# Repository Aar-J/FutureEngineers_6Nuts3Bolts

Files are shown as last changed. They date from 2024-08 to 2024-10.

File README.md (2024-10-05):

# Welcome to our GitHub!

# Introduction
We are team 6Nuts3Bolts, a dynamic trio of passionate robotics enthusiasts. 
Based off of the nature of the task, we divded the industry and each took on a key aspect of the challenge.

**Arham**: 

He is in charge of the electronic systems as well as the documentation.

WhatsApp Image 2024-10-04 at 6 19 59 PM

**Shauryaveer**:

WhatsApp Image 2024-10-04 at 6 20 24 PM

He is our main designer and constructor and worked on the car's mechanisms

**Ranveer**: 

WhatsApp Image 2024-10-04 at 6 20 25 PM

He is our programming lead, and responsible for all the code and processing on our robot.

**Team Photo**:

Untitled design (48)

Untitled design (49)

# Table of Contents
Car photos

Vehicle Videos
- Open Round
- Obstacle Round

Our Engineering Process

- Fundamental Parameters
- Mobility Management
  - Explanation
  - Iteration Process
  - How we achieved our target
  - Improvements
  - Parts list

- Power and Sense Management
  - Explanation
  - Iteration Process
  - How we achieved our target
  - Improvements
  - Parts list
    
- Obstacle Management
  - How we achieved our target
  - Explanation
  - How we achieved our target
  - Future Improvements
  
Acknowledgement to our mentor Sahil Gajera Sir

Thank you to the judges

# Car Photos

### Top View

Untitled design (42)

### Bottom View

Untitled design (43)

### Front View

Untitled design (44)

### Back View

Untitled design (45)

### Left side 

Untitled design (46)

### Right Side

Untitled design (47)

# Vehicle Videos
### Open Round
https://www.youtube.com/watch?v=metChoJu9pQ

### Obstacle challenge
https://www.youtube.com/watch?v=metChoJu9pQ

# Our Engineering Process
We have used scoring criteria from the ruleblock as headings in our documentation to make it easy to navigate our repository.

It is vital to understand a problem and its features in depth before planning and undertaking its solution. Hence, we first spent a day analysing the challenge in depth and noting down a few principles, parameters, fundamental ideas off of which we could organize our thinking and streamline our ideation process to efficiently solve the challenge. 
Here are the principles we decided on:

## Fundamental Parameters
**Design and Construction**
- Compact, able to maneuver past obstacles even at high speeds
- Simple and practical, a design appropriate for the challenge, not overly complex
- Modular, quick and easy to assemble and disassemble

**Electrical Systems**
- Clean and orgranised, connections easy to keep track of
- Reliable and safe, eliminate any chances of a short or circuit failure
- Easy to assemble and dissassemble

**Logic and Programming**
- Simple and organized
- Easy to navigate, debug and troubleshoot
- Flexible, able to evolve easily to overcome any issues or edge cases

Based off these fundamental ideas, we aimed to conceptualize our robot.
Next, we immediately begain the prototyping and iteration process.

Here's how we went about turning our vision into reality

## **Mobility management**

### Explanation

**Why we chose the RevRobotics NEO550**

Untitled design (15)

- It has an absolutely phenomenal power to weight ratio (weighing only 140grams and has a peak output power of 279W) as well as very high acceleration and has a free running speed of upto 11000 RPM.   We have geared it in a 5:1 ratio. This can further be seen through this graph

Untitled design (59)

- We had previously used this motor in FRC (FIRST Robotics Competition) and hence were comfortable operating with it.
- It has excellent speed control and is easy to integrate and program with the SparkMax motor controller.
- We had initially considered making a smaller robot and at the time had considered using an N20 500 RPM Encoder motor, however this placed a lot of restrictions on our other electronics and design. We also considered using a standard Johnson 500 RPM motor, or a TT Gearbox motor however we rejected these for similar reasons as well as the fact that the NEO 550 just outclassed all 3

**Why we chose MG996R Servo**

Untitled design (17)

- It is a popular and reliable servo which for us is delivering about 9.5kgcm(since we are powering it through the RaspberryPi 5V pin)
- It is easily able to steer our robot even at high speeds.
- The position accuracy it is able to provide is relaible and it is able to steer at a rate of about 0.30 sec/60° degrees according to our measurements.

**Electronics Mounting Plate** 

Untitled design (22)

Untitled design (29)

The electronics table offers ample space for organizing wiring effectively. It is spacious enough to accommodate most of the wiring, ensuring everything remains well-organized and accessible for easy maintenance and troubleshooting.

**Top Plate**

Untitled design (23)

Untitled design (31)

The top plate is the strongest and most robust part of the robot, serving as its backbone. 

It plays a vital role in every subsystem, providing structural integrity and supporting the entire design.

**Bottom Plate**

Untitled design (24)

Untitled design (30)

The bottom plate provides essential support and serves as a key aesthetic feature for the robot. It protects the belly of the robot from potential damage while also adding significant structural integrity to the overall foundation. By ensuring a strong base, the bottom plate helps maintain the robot's durability and stability during operation. Its role in reinforcing the lower framework makes it a critical component of the robot's design.

**Bevel Gears**  

Untitled design (25)

Untitled design (32)

The bevel gears are designed for durability, featuring a large diameter and sizable teeth. This design ensures they wear out more slowly, making them reliable and long-lasting components of the drive system.

**Motor Bracket**  

Untitled design (26)

Untitled design (33)

The motor bracket is small and simple in design, effectively performing its function without occupying excessive space. 
It optimizes space utilization while ensuring the motor is securely mounted.

**Camera Mount**  

Untitled design (28)

The camera mount is tall and adjustable, providing flexibility in positioning without taking up much flat space on the electronics table. It offers several customization options to fit various configurations as needed.

**Steering System**  

Untitled design (27)

Untitled design (34)

The steering system is compact and straightforward, featuring a linkage-based design. It allows for the maximum possible steering angle and is highly reliable, ensuring excellent maneuverability and performance.

### Iteration process
We went through 4 iterations of the design. Here's a bit about them.

**Version 1**



We began with a simple, open chassis design that provided ample space for future electronics and cabling, offering flexibility to adjust the layout as needed.

The motor and electronics were placed centrally to maintain balance and reduce the risk of tipping during movement.

The flat and spacious base was designed to simplify assembly and allow easy access to key components.

For the steering system, we initially used an approximate Ackermann configuration to improve cornering performance by adjusting wheel angles based on turning radius.

After evaluating the robot’s performance, we switched to a linkage-based steering system, which offered more straightforward control with fewer mechanical components, minimizing potential points of failure.

We integrated the bulky Limelight camera, mounting it high on a custom bracket to ensure optimal visibility for the robot's vision systems.

Although the camera’s size was disproportionate to the compact robot, we relied on it for initial tests due to its accuracy in target detection and our team's familiarity with its setup.

The camera placement was chosen to minimize interference from the robot's body and ensure accurate visual data capture.

This design iteration allowed us to explore several improvements for future versions, including lowering the base height to reduce the robot's center of gravity and increase stability,
transitioning to a layered architecture for better component arrangement and improved separation of electronics, minimizing signal interference, and
trimming excess space in the length and width of the frame to create a more compact and efficient design, maximizing maneuverability without sacrificing functionality.

**Version 2**



In this iteration, we focused on making the design more compact and practical, even if it introduced some complexity.

Unlike the modular and adjustable nature of Version 1, this design was fully customized for the specific requirements of the use case.

The first major decision was to align the motor with the length of the robot, significantly reducing the overall width.

To achieve this, we implemented a 90-degree power transmission system using custom-designed, 3D-printed bevel gears (approx. 2 cm in diameter).

The custom motor mount could also house a REV Through Bore Encoder to measure back wheel rotations, but we decided it wasn’t necessary for this version.

We introduced a layered structure with three levels:

The top layer was exclusively for the electronics.

The lower layers housed wiring, the SPARK MAX controller, and other components.

After finalizing the battery choice, we built the robot layout around it to ensure proper space allocation and balance.

The electronics board was designed to be hot-swappable, allowing it to snap into place without screws, so electronics development could be done separately and easily integrated.

We also implemented a simple linkage-based steering system, powered by the MG996R servo, improving steering control while keeping the design compact and efficient.
The transition from Version 1 to Version 2 marked a significant leap, making the robot more space-efficient and purpose-built for the specific application.

**Version 3 (Abandoned)**



In this version, we aimed to make the robot as small as possible, accommodating every element efficiently.

The chassis width was reduced to 8.4 cm (down from 10 cm), significantly improving maneuverability.

The overall height was also reduced, and although ground clearance wasn’t a priority, it was slightly improved for potential ground-facing sensors.

Early in the design, we realized shrinking the dimensions came with trade-offs.

The maximum turning angle of the steering wheels was reduced by 10-15 degrees on either side.

The servo had to be placed in an unconventional manner.

To address these issues, we explored adding 5-6 layers to the design to distribute components while keeping the robot compact.

Despite our efforts, feedback from testing Version 2 showed that width wasn’t a major concern, and while this version was sleeker, it presented too many complications.
The layered structure created challenges in both assembly and component access, making the design overly complex.

From this iteration, we learned that the current dimensions were already optimized, and future designs would likely stay within a tolerance of ±2-3 cm.

Making the robot smaller worsened the wiring complexity, as the compact spaces made routing cables and connections more difficult to manage.

This realization helped us pivot back to a more practical sizing while still focusing on overall efficiency.

**Version 4**



In this version, we started from scratch, incorporating lessons from previous iterations.

The width remained unchanged, but the length was significantly reduced.

We transitioned from a 20:1 UltraPlanetary gearbox to a 5:1 system, which, along with steering modifications, allowed us to achieve our most compact design yet.

The electronics table at the top was made wider, extending beyond the chassis but staying within dimensional constraints.

We moved away from the hot-swappable top plate design, as the snap-on system weakened after repeated use and occasionally broke off.

The bottom plate was refined to remove unnecessary parts and featured our team name cut out for weight reduction and aesthetic appeal.

The middle plate now carried the bulk of the structural load, becoming the backbone of the robot. The thickness of both the bottom and middle plates was increased from 3mm to 4mm, greatly improving strength and eliminating flex.

A key improvement was in the drive subsystem, during test runs, we noticed vibrations while turning, due to the lack of a differential system.
The inside and outside wheels rotated at the same speed, causing a mismatch.
To fix this, we reduced the gap between the wheels, minimizing vibration in a simple manner.
We also upgraded the bevel gears, increasing their size from 2 cm to 3 cm in diameter.
This made the gears much stronger, eliminating wear-and-tear issues.

Previously, we had to replace the smaller gears after every five runs, but with the new design, frequent replacements were no longer necessary.

Overall, this design marked the culmination of all our ideas and refinements, making it the most optimized and efficient version yet, combining technical improvements with practical design choices.

**Key Differences between the versions**
| **Aspect** | **Version 1** | **Version 2** | **Version 3 (Abandoned)** | **Version 4** |
|---|---|---|---|---|
| **Chassis Design** | Simple, open chassis with spacious flat base for flexibility | Compact and customized, 90-degree power transmission via bevel gears | Extremely compact, 8.4 cm width; 5-6 layered design; trade-offs in turning radius | More compact than v2, width unchanged, reduced length |
| **Motor Placement** | Central for balance | Aligned with the length, bevel gears for 90-degree power transmission | Motor placement compromised for size | Same as v2, with more robust gearing system |
| **Steering System** | Approximate Ackermann, later switched to linkage-based | Linkage-based, powered by MG996R servo | Reduced turning angle due to compactness | Linkage-based with further steering modifications to reduce size |
| **Electronics Layout** | Spacious, simple arrangement on a general-purpose board | Layered design with three levels, hot-swappable electronics board | 5-6 layers proposed, overly complex, compact | Wider electronics table, no hot-swappable design due to durability issues |
| **Camera System** | Limelight camera, large and mounted high for optimal visibility |Limelight Camera Swapped for RaspberryPi Camera| Same as v2, camera mount strengthened | Same as v3 |
| **Frame Dimensions** | Spacious, flexible for adjustments | Narrower (due to motor alignment) and more layered | Extremely compact (8.4 cm width), but overly complex | Reduced length, width unchanged; optimized overall dimensions |
| **Gearbox** |20:1 UltraPlanetary gearbox |Same as v1 | Same as v2 | Switched to 5:1 UltraPlanetary gearbox for compactness and speed|
| **Bevel Gears** | Not used | 2 cm diameter, custom 3D-printed | Same as v2, but layering increased difficulty | 3 cm diameter, stronger, reduced wear and tear |
| **Material Strength** | Standard 3 mm plates | Standard 3 mm plates | Same as v2 | Plates increased from 3 mm to 4 mm for improved structural strength |
| **Vibration Control** | We discovered the vibration issues | No differential system, resulting in vibrations | Working on v4 since v3 was abandoned| Reduced wheel gap to minimize vibrations during turns |
| **Testing and Feedback** | Preliminary tests with bulky camera setup | Refined design with specific components, partial finalization | Abandoned due to complexity, compromised steering, and wiring issues | Final optimized version, most refined in terms of design and performance |
| **Complexity** | Simple and flexible | More complex but optimized for purpose | Extremely complex and impractical | Balanced complexity with practical refinements |

### How we achieved our target

**How we made it Compact**

More well positioned Cardboard Plate (3)

We began by visualizing how all the components could fit closely together, and we built around that idea. The space between parts is minimal, but we made sure it wouldn’t create any issues in performance or accessibility.
The overall length of the robot is limited by key components like the NEO 550 motor, bevel gears, and the steering system, while the width is determined by the size of the Spark MAX, ultrasonic sensor, servo, and battery. By carefully balancing the length and width, we were able to create a robot that is compact yet fully functional. The width isn't constrained by any specific part, it’s simply as wide as necessary to accommodate the essential components.

**How we ensured simplicity and practicality**

From the beginning, we adopted a mindset of keeping things simple. We've learned that complexity can quickly lead to chaos, especially when time is tight or you're troubleshooting under pressure. By focusing on simplicity, we narrowed our options and only considered ideas that were practical and easy to implement. If a solution met our goals without adding unnecessary complications, we ran with it. Simplicity also naturally led to practicality because fewer moving parts meant fewer things to go wrong, and every design choice was intentional and straightforward.

**How we made it Modular**

The entire robot is based around three main plates, with each subassembly between them individually 3D printed. This modular design gives us a lot of flexibility. In case something goes wrong with a specific part, we don’t need to overhaul the entire system—just swap out the problem area. It makes troubleshooting and maintenance much quicker and less stressful.
We designed the robot to be broken down into three key systems: the drive system, the steering system, and the electronics assembly. Any part that doesn’t fall into one of these categories is mostly there to provide structural integrity and support to the main components. For instance, the bottom plate doesn’t serve any critical function other than strengthening the overall structure. This modular approach ensures that our robot remains easy to work on, upgrade, and maintain, which is key for long-term reliability.

### Future Improvements
If we had more time, we would likely explore a more complex design that branches off from the v3 concepts while integrating elements from the v4 robot. This hybrid approach would allow us to capitalize on the strengths of both iterations, leading to an ideal robot that embodies our design philosophy. By merging the compact efficiency and structural integrity of v3 with the advanced features and refined functionality of v4, we could create a robot that maximizes performance while enhancing maneuverability and adaptability. This exploration could involve developing a more sophisticated drive system or experimenting with innovative materials and configurations to further reduce weight and improve responsiveness. Ultimately, this integration of ideas would help us push the boundaries of our design capabilities and achieve our vision of an optimal robot tailored to our specific needs.

### Hardware Components list:
- Rev Duo 60mm Traction Wheels https://www.revrobotics.com/DUO-Traction-Wheels/
- **Chassis**
  - **Top plate**
  - **Bottom Plate**
- **Steering Mechanism**
  - **Linkage**
  - **Left Front**
  - **Right Front**
- **Bevel Gears**
- **Motor Bracket**
- **Electronics Mount**
- **Camera Mount**
- **1 x Servo horn** (comes with servo)
- **20 x m3 10mm bolts** https://robokits.co.in/robot-parts/nut-bolts-standoffs/allen-cap-socket-head-bolts/m3-x-10-mm-socket-head-cap-stainless-steel-304-bolt-moq-15-pcs
- **2 x m3 30mm bolts** https://robokits.co.in/robot-parts/nut-bolts-standoffs/allen-cap-socket-head-bolts/m3-x-30-mm-socket-head-cap-stainless-steel-304-bolt-moq-15-pcs
- **16 x m3 nyloc nuts** https://robokits.co.in/robot-parts/nut-bolts-standoffs/nuts/m3-nyloc-nuts-304-stainless-steel-moq-25-pcs
- **1 x 90mm shaft** https://www.revrobotics.com/5mm-Hex-Shafts/#REV-41-1348-PK4
- **1 x 20mm shaft** (can be cut from longer shaft)
- **2 x shaft collars** https://www.revrobotics.com/rev-41-1327-pk10/
- **4 x 60mm rev wheels** https://www.revrobotics.com/DUO-Traction-Wheels/#REV-41-1350-PK4

## **Power and sense management**

## **Explanation**

### Reason for choice of parts

**RaspberryPi 4B**

Untitled design (35)

- With its quad-core ARM Cortex-A72 64-bit 1.5GHz processor and 8GB RAM it meant that we would never face a computationl bottleneck, even with the heavy task of image processing in the obstacle         challenge.
- Its ability to be programmed and controlled wirelessly was a boon during the testing and debugging phase as we could run the robot almost continuously without having to detach and reattach            the cable for uploading code.
- Its extensive use and testing was the reason we chose to go with the RaspberryPi 4B instead of the newer RaspberryPi 5. If there was ever an issue we faced, it could most likely be solved by          searching up the problem.

**RaspberryPi Camera Module 3 with Wide Angle lens**

Untitled design (36)

- We chose this mainly for its ease of integration and compatability with the RaspberryPi. 
- Its wide FOV (120 degrees), high resolution(12 megapixels), autofocus feature and ability to sense color in a wide range of lighting conditions allowed for efficent obstacle detection and             sensing from varying distances and angles even while moving at high speeds

**Arduino Nano**

Untitled design (37)

- The use of the Arduino Nano in our robot is solely to gather data from the ultrasonic sensors and relay it to the RaspberryPi. 
- Hence its compactness and low power consumption was the main reason we chose to use it.

**BNO055 IMU**

Untitled design (38)

- The BNO055 is a highly tested and reliable sensor. We had used it earlier in FTC(First Tech Challenge) as well as in a drone we made. We had also used it in Future Engineers the previous year.
- It has an inbuilt sensor fusion algorithm and it is easy to integrate with the RaspberryPi, communicating over I2C.

**RevRobotics SparkMax Motor Controller**

Untitled design (18)

- Using the NEO550 meant we would have to use this since they are complimentary pieces of hardware.
- Its inbuilt current limiting feature also allows for the motor to remain safe from sudden power surges.

**HC-SRO4 Ultrasonic Sensors**

Untitled design (14)
- These are widely available and a popular choice of sensor although sometimes they may be unreliable, with good programming they can be made to work just fine. 
- There are many resources and libraries available online to control these effectively making both programming and troubleshooting easy to do.
- Their accuracy is reasonable, able to provide output within a 2-3mm range of error and are also able to maintain consistency at moderate speeds, providing data every 30ms.
- Apart from that, its also easy to integrate

**Xcluma USB Buck Converter**

Untitled design (16)

- It was able to provide a more stable output of 5V than the buck converter we were previously using. It also made it such that we could easily power the RaspberryPi through its USBC port.
- It was also more compact than the previous buck.
- Its built in safety feature of preventing against overvoltage and overcurrent proved to be useful especially during testing.

**2200MAh 40C 12V LiPo Battery** 

Untitled design (39)

- We needed a high power battery since the electronic components we used(RaspberryPi while image processing, NEO550) were quite power hungry.
- It was also capable of providing our robot with a long runtime. We can run our robot for 12 minutes continuously.

### Circuit Schematic

WRO Future Engineers Circuit Schematic

### Iteration Process

**Version 1**

This was a prototyping version, simply to test the circuit and have a robot capable of moving while we worked on a better one. This was for version 1 of the design.
It consisted of the Electronics mounted on a cardboard plate and the use of a prototyping board fundamentally composed on 4 buck converters. There were wires going everywhere, even outisde the perimeter of our bot. However, this was only ever meant to be a prototyping version. 

Carboard Plate (1)

**Version 2**
This was also merely a prototyping version intended on having a functional robot to program. The difference between Version 1 and 2 is solely the cleanliness of the mounting and the organization of wires. This was mostly in place during versions 2 and 3 of our desgn

The Crius power distribution board was a cool piece, however it was ultimately redundant. It consumed space, as well as had excess ports which we had no use for. Hence it was discarded. 
The fuse we were using had a rating of 15A. Our circuit will never draw more than 4A hence this was also unnecessary.
The cardboard plate mounting although humble, actually surprised us as it turned out to be quite solid and reliable. However we  knew that having a proper circuit board would yet be a better decision.

More well positioned Cardboard Plate (2)

**Version 3**

Untitled design (60)

We were always planning on soldering all the components onto one single board for the final iteration of our robot, however due to changes in components as well as troubleshooting, we waited till all our systems were finalised before making our circuit board. This is what we used for version 4(final) of our design

This is (at leat for nationals) the final iteration of the electrical systems of our robot. It is a significantly improved version and has all the electronics mounted on a general purpose board. It provides a clean and professional look to our robot and also minimises wiring mistakes as well as chances of shorts. 

### **How we achieved Clean and Organized wiring**

To keep our wiring system easy to manage, we focused on clarity, organization and structure in all connections.

More well positioned Cardboard Plate (4)

We used solid core wire for connections since they can be bent into shape making wiring neat and easy to solder.
We soldered all wire connections and mounted them on a general purpose board providing a solid foundation for the wiring, minimizing loose wires and clutter.
Every wire was labeled and color-coded, making it simple to track individual connections. This helped ensure quick identification of components during assembly and troubleshooting.
  
Red - VCC wires 🟥

Black - GND wires ⬛

Purple - PWM Signal (Pin 33 or GPIO 13 on RaspberryPi) 🟪

Yellow(Ultrasonic) - TRIG (Pins D3 and D7 on Nano) 🟨

Blue(Ultrasonic) - ECHO (Pins D4 and D6 on Nano) 🟦

Yellow(BNO055) - SDA (Pin 3 or GPIO 2 on RaspberryPi 🟨

Blue(BNO055) - SCL (Pin 5 or GPIO 3 on RaspberryPi) 🟦

Blue(Button) - SIGNAL (Pin 11 or GPIO 17 on RaspberryPi) 🟦 

Black and White Dual Wire(SparkMax Communication) - ⬛⬜ (Pin 33 GPIO 18 and Pin 34 or Ground)
    
### **How we ensured Reliability and Safety**

We took extra care in insulating all exposed connections to prevent shorts or malfunctions. 

Untitled design (53)

This was done to all soldered connections by applying heat-shrink tubing, hot gluing wire ends and using 
electrical tape wherever required for additional protection and to reinforce connection stability.
We used barrier terminal blocks and JST connectors which hold the wires firmly in place thus preventing them from moving around and accidentally causing short circuits or bending of wires.
Wago connectors were used for connections between the SparkMax and Neo ensuring a tight and insulated fitting.
    
### **How we made it convenient to assemble and dissasemble**

Untitled design (61)

Ease of maintainence and assembly was another top priority. 

We soldered header pins onto the general purpose board in order to render the Arduino Nano, BNO055, and servo easily detachable and replaceable.
The screw in nature of the barrier terminal blocks not only added a layer of security to our electrical system but also served as a way to ensure quick maintanence. The wires can be removed and reattached by simply screwing and unscrewing the terminals. 
A similar story is for the the JST connectors, their ability to snap in place makes it easy to attach and detach the ultrasonic sensors.
Wago connectors are convenient to make connections with components where cutting the wiring and making solder joints is not preffered due to the wire being inbuilt into the component like the SparkMax and NEO550.
We also used crimp connectors for the switch, such that we could quickly remove and replace it if necessary since we had faced issues during practice of the switch being unreliable

### Future Improvements

- We plan on using PCB Design software to create a circuit design and then have that PCB printed and manufactured. This will almost completely eliminate     small wired connections and chance of circuit failure.
- We also plan on swapping out the HC-SR04 Ultrasonic sensors with faster and more reliable ones like the URM09 or SEN001.
- We may also swap out the RaspberryPi for a more powerful controller like the Jetson Nano

### Electrical Components list:
- **RaspberryPi 4B**
  https://robu.in/product/raspberry-pi-4-model-b-with-4-gb-ram/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
  
- **Raspberry Pi Camera Module 3 with Wide Angle Lens**
   https://robu.in/product/raspberry-pi-camera-module-3-wide/
  
- **Arduino Nano**
  https://robu.in/product/arduino-nano-board-r3-with-ch340-chip-wo-usb-cable-solderedarduino-nano-r3-wo-usb-cable-soldered/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        
  gad_source=1&gclid=CjwKCAjwgfm3BhBeEiwAFfxrG2RzmpzoTJQA5ThT4OKJQDOLGdDu_CcdCzMTJhiYnkzNB_LoFYl8ChoCa28QAvD_BwE
  
- **BNO055 IMU**
  https://evelta.com/7semi-bno055-9-dof-absolute-orientation-sensor-breakout-i2c-qwiic/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
  
- **MG996R Servo**
  https://robu.in/product/towerpro-mg996r-digital-high-torque-servo-motor/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
  
- **RevRobotics NEO550**
  https://www.revrobotics.com/rev-21-1651/
  
- **RevRobotics SparkMax Motor Controller**
  https://www.revrobotics.com/rev-11-2158/
  
- **HC-SR04 Ultrasonic Sensors**
  https://robu.in/product/hc-sr04-ultrasonic-range-finder/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
  
- **Xcluma USB Buck Converter**
  https://www.xcluma.com/0.9v-5v-to-5v-600ma-usb-output-charger-step-up-power-module-mini-dc-dcboostconvertergad_source=1&gclid=CjwKCAjwgfm3BhBeEiwAFfxrGwnZnr6HztAhUfI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
  
- **2200MAh 40C 12V LiPo Battery**
  https://robokits.co.in/batteries-chargers/drone-batteries/genx-power-premium-lipo-battery/genxpower-11.1v-lipo-batteries/genx-11.1v-3s-2200mah-40c-80c-premium-lipo-l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
  
- **Switch**
  https://robu.in/product/kcd5-101-mini-rocker-switch-2pinon-off/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
  
- **Pushbutton**
https://robu.in/product/mc002076-terminal-block-barrier-3pos/
  
- **General Purpose Board**
  https://robu.in/product/8-x-12-cm-universal-pcb-prototype-board-single-sided-2-54mm-hole-pitch/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
  
- **JST Connectors**
  https://robu.in/product/4-pin-jst-xh-2-54mm-pitch-plug-and-socket-with-cable-5-pcs/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
  
- **Jumper Wires**
  https://www.amazon.in/Electrobot-Jumper-Wires-120-Pieces/dp/B071VQLQQQ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
  
- **Solid Core Wires**
  https://robocraze.com/products/single-stranded-hook-up-wires-1m-each-5-colorsvariant=40193905590425&currency=INR&utm_medium=product_sync&utm_source=google&utm_conten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
  
- **XT60 Connectors**
  https://robu.in/product/amass-xt60-male-connector-xt60-m-g-y/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
  
- **Crimp Connectors**
  https://www.tsktech.in/product/6-3mm-female-spade-connector-with-insulator-boot-crimp-terminal-thimbles-no-color-choice-pack-of-10nos/
  
-**Wago Connectors**

 https://www.flipkart.com/wago-2-conductor-compact-inline-splicing-connectors-electrical-wire-connector/p/itmd8735b383bb17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

## **Obstacle management**
In this sections first we will first discuss how we solved the obstacle challenge and then move onto the  solution for the open round challenge as well as a general explanation of our software and logic flow.

### Explanation

#### **Obstacle Challenge**

First we begin by importing all the libraries



import time 
- The time library, as the name suggests allows us to use time related functions like delays.



import board
- Its use is primarily to access pins on the RaspberryPi.



import busio
- This library allows us to access external buses and serial protocols allowing for hardware acceleration on the RaspberryPi.



import adafruit_bno055   
- Library for BNO055 IMU sensor



import sys
-  This library basically allows us to run functions and call from different files and parts of code. Its gives us commands to access system related variables and functions.



import serial  
- This allows for serial communication with external devices. We communicate with the Arduino Nano over serial



sys.path.append('/usr/lib/python3/dist-packages')  
- We have created custom packages for the left journey and right journey of the open round. Both are called. The robot must decide which one to run.


  
import pigpio   
- The RaspberryPi's software PWM signal is often unstable and unreliable. The pigpio library solves this issue generation a hardware PWM on the the         
  RaspberryPi.



from picamera2 import Picamera2, Preview  
- Camera library for handling the Raspberry Pi camera



import cv2  
- Here we are importing OpenCV for camera processing and display. This handles all of the vision processing.



import numpy as np
- Here we import NumPy for numerical operations using it in conjunction with OpenCV for image data processing.



import Blue_detected as b1
- This is a custom module containing functions for color detection.

Next we set up all the communication protocols, declare all the control variables in our program and initialise the necessary objects. 
We will use these to build our logic.



- We create a Picamera2 object to handle camera operations.
  
- The video configuration is set to a resolution of 640x480 pixels, with a frame duration limit of 33.33 milliseconds, which corresponds to 30 frames per second.
  
- The camera is then started, preparing it to capture images.



pi = pigpio.pi() 
- Initializes the pigpio library for GPIO control



pi.set_mode(18, pigpio.OUTPUT)  
- Set GPIO pin 18 as an output (for NEO550 Motor)
  
pi.set_mode(13, pigpio.OUTPUT) 
-  Set GPIO pin 13 as an output (for MG996R Servo)



i2c = busio.I2C(board.SCL, board.SDA)   
- Initializing I2C bus for communication with the IMU



ser = serial.Serial('/dev/ttyACM0', 9600)  
- Setting up a serial connection to an external device (Arduino Nano) at 9600 baud rate



sensor = adafruit_bno055.BNO055_I2C(i2c)  
- Initializing the BNO055 sensor using I2C



heading = 0.0   
- To store the heading (direction) from the IMU sensor


  
dis = 0.0  
- To store the distance from the left sensor
  

 
value = 360 
- Value to control servo/motor position



count = 0  
- A counter to count number of loop iterations



arR = arG = yy = xg = xr = 0
- These are variables for color detection areas.



orange = False
- Flag variable for if orange color is detected.



increment = False  
- Flag for controlling incremental behavior



flag = True  
- Flag variable to track state



init = True  
- Flag variable to track initialization state

PID Controller

Here we initialise our PID function



The input parameters for the PID Controller are :

**y** 
- This is the target heading or the direction you want the robot to face.
  
**heading** 
- This stores the current heading of the robot, i.e., the direction the robot is currently facing, measured by the BNO055 sensor.
  
**kP**
- This represents the proportional constant used to determine how much correction to apply based on the error. The higher the constant, the more   
  aggressively the robot will correct its heading.
  


Here we normalize our "y" or target heading.
- This part ensures y is normalized within the range of -180 to 180 degrees.
  
- The idea is to convert the heading into a more manageable format that can be used for comparison and calculation.
  
- If y is less than 360 - y, it remains unchanged.
  
- If y == 360 - y, meaning it’s exactly opposite (180 degrees), it's set to 180 degrees.
  
- Otherwise, it subtracts y from 360, effectively flipping it to the opposite direction.

  

Similarly, this block normalises our current heading.

In this block, we calculate our error.



- Error is the difference between the current heading and the target heading.
  
- This error is used to determine how much the robot needs to adjust its steering to correct its path.
  
- There are three conditions:
  
  - Both headings are negative: The error is simply the difference between heading and y.
  - Heading is negative, but the target is positive: The error is the sum of y and heading.
  - In all other cases: The error is calculated as the difference between heading and y.

Based off this, we calculate our turn value and return it.



- This line calculates the servo pulse width for the robot’s steering servo based on the error.

- The idea is to adjust the robot’s steering proportionally to the error, which means the bigger the error, the bigger the correction.

- The formula is: 1200 - error * kP, where 1200 is the neutral position (centered steering), and error * kP is the correction based on how far off the 
  heading is.

- To prevent extreme values, the min and max functions are used to clamp the output between 800 and 1600. These limits ensure that the servo doesn’t exceed 
  its physical range

This is the main control loop for image capture and processing.



Image Capture:

- The camera captures an image array into img.

Image Processing:

- Color Conversion: The image is converted from BGR to RGB format for compatibility with the OpenCV functions.
  
- Color Detection: The program calls color detection functions from the Blue_detected module:
  
- red_detect(img): Detects red areas in the image and returns the image with markings, along with the area (arR), and coordinates (xr, yr).
  
- green_detect(img): Similar function for detecting green areas.
  
- color_detect(img, lower, upper, "blue"): Detects blue areas with specified lower and upper color thresholds.
  
- A second call to color_detect is used to detect orange areas, with specific HSV values.

Display:

- A white rectangle is drawn on the top part of the image frame for visual guidance, and the processed image is displayed in a window titled “frame.”

In this block, we retrieve sensor data.



- The robot finds its current heading, roll, and pitch from the BNO055 sensor's Euler angles.
  
- The heading is clamped to ensure it stays within the range of 0 to 360 degrees.
  
Distance Measurement:

- The program reads a line from the serial port, decoding it to a string. It expects distance data in a comma-separated format.
  
- The data is split into two float values, representing distance measurements (dis for one side and distanceRight for another side).
  
- If reading fails, both distance values are defaulted to 0.

This block contains the color processing logic.



- The code checks the areas of detected colors:
  
- If the detected area for blue (yy) is between 100 and 250, it sets the flag blue1 to True.
  
- If yy exceeds 340, it sets another flag blue2 to True.
  
- The robot checks if both blue flags are set and if an orange area (yy2) is detected. If so, it sets the orange flag to True, indicating that it can 
  respond to the orange color.

Next we have the Servo control logic.



- If a significant red (arR) or green (arG) area is detected (both with area thresholds), it sets the flag to True and resets orange to False.
  
- If the orange flag is set and the distance (dis) is greater than 15, it executes specific logic for turning towards orange.
  
Default Case:

- If no significant colors are detected, it defaults to adjusting the servo's pulse width using the PID control function.
  
- If increment is True, it increments the count and resets the increment flag, allowing for controlled execution across multiple iterations.

Lastly we have the stopping procedures



- This stops all active servo and motor operations by setting their pulse width to 0, effectively disabling them.
  
- All OpenCV windows are closed to free up resources.
  
- The camera is stopped, ensuring it is no longer capturing or processing images.
  
- The pigpio connection is released, completing the stopping process.

  This is how we solved the Obstacle Challenge.

#### **Open Round**

**Logic Flowchart**
  
algorithm_flowchart

The setup of the libraries and pins and communication protocils for the Journey Right and Left programs is the same as the obstacle challenge, minus a few hence, explaining that once again would be redundancy.

Only the left and right journey programs need to be imported here seperately.



import JourneyLeft as l  # Custom module to handle left-side journey logic
import JourneyRight as r  # Custom module to handle right-side journey logic
- These are the Journeys we made for either running the robot clockwise or counterclockwise. Their explanation is just after.



logic = False  
- Flag variable for decision logic, to decide whether to run left journey or right journey



left = 0  
- Flag variable to track whether the robot is turning left or right



time.sleep(3)  
- Delay for 3 seconds before starting the main loop

Now we come to the main loop of our program.



- The main loop runs as long as count is less than 3.
  
- sensor.euler: Reads the Euler angles from the BNO055 sensor, including the heading (yaw). We calculate our error based off this value

- The try-except block ensures the heading stays within the range of 0 to 360 degrees. If there's an error in reading the sensor, the heading is set to 0.
  
- ser.readline(): Reads a line of distance data from the Nano.
  
- The try-except block attempts to split the incoming data into two values (dis for the left distance and distanceRight for the right distance). If parsing 
  fails, both distances are set to 0.

Within this loop we have 3 logics:
1. Left and right journey Logic

   

- If the robot is set to move left, (left == 1), then it calls the L_journey() function from the JourneyLeft module, which handles the logic for left-side movement. The function returns updated values for value, logic, flag, etc.
  
- Similarly, if the robot is set to move right, (left == 2), it calls the R_journey() function from the JourneyRight module, which handles the logic for   
  right-side movement.
  
- The variable init ensures that certain behaviors only happen on the first run of the loop.

2. Distance Comparison Logic
   
   

- If the left distance (dis) is greater than the right distance and both are more than 100 cm, the robot turns left by calling the L_journey() function.
  
- Similarly if the right distance is greater than the left, the robot turns right by calling the R_journey() function.
  
- This logic ensures the robot chooses which direction to move based on sensor readings.

3. Default(Straight movement) and exit logic
   
   

- If the robot is neither turning left nor right, it calls the default move() function from the JourneyLeft module, which handles straight-line movement.
- The cv2.waitKey(1) function listens for keyboard input. If the user presses 'Q' or 'q', the loop exits, stopping the robot.

Final actions after the loop:



- After the loop ends, the robot performs a final stopping movement.
- pi.set_servo_pulsewidth(13, 0) stops the servo or motor connected to GPIO pin 13 by setting the pulse width to 0, ensuring the robot halts.

Here's an explanation of the journey logic explained using the example of the Journey Right program.

The setup of the libraries and pins for the Journey Right and Left programs is the same hence, explaining that once again would be redundancy.

Finally, this is the R_Journey function



This section resets the variables when the journey starts.
We also display our enthusiasm upon its initialisation.

In case we encounter a large right distance, we handle it in this block



- If the right distance is large (>= 120 units), or the robot is already turning (logic flag is True), it adjusts the desired heading (value) by 90 degrees.
  
- If value reaches 360, it is reset to 0.

Here is our Steering logic.



- If the current heading is not within a certain range of the desired heading, the robot adjusts its turn.
  
- The servo_pulsewidth for GPIO 18 controls the motor's speed for forward movement.
  
- pi.set_servo_pulsewidth(13, 1570) is set to control steering based on the difference between the current and desired heading.

Lastly we have the straight movement case.



- If the robot is not turning, it moves forward, and the PID controller is used to ensure the robot stays on course.
  
- Servo Control: The pid function is called to calculate the pulse width for steering correction.

### How we achieved our target

- We started with a simple logic consisting of an if else ladder to maneuver right around red and left around a green block and to take turn when it detected a line. This logic at the core kept the code simple and flexible
- We mostly focused on our detection logic ensuring our robot would be able to detect the obstacles and make the correct decisions even at high speeds
- We realised the key to solving the challenge lay primarily in repetitive testing and updating the code handling all the edge cases that came our way. 

### Future improvements

# Acknowledgement to our Mentor Sahil Gajera Sir

Untitled design (58)

We would like to express our gratitude to our mentor Sahil Gajera Sir for his invaluable technical guidance throughout the competition.
Moreover, his constant encouragement and unwavering moral support motivated us to push our limits and stay focused. 
Thank you, Sir, for being an incredible mentor!

# Acknowledgement to our esteemed Judges

We would like to extend our sincere thanks to the esteemed judges for taking the time to review our engineering notebook with such care and patience.
We greatly appreciate your dedication to guiding us through this process and for the opportunity to showcase our efforts and passion for technology. 
Thank you for contributing to our development as future engineers!

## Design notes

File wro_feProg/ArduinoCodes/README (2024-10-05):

This contains the code for the ultrasonic sensors which are wired to the Arduino Nano.
Their values are obtained on the serial monitor which is called in the OpenChallenge RaspberryPi code

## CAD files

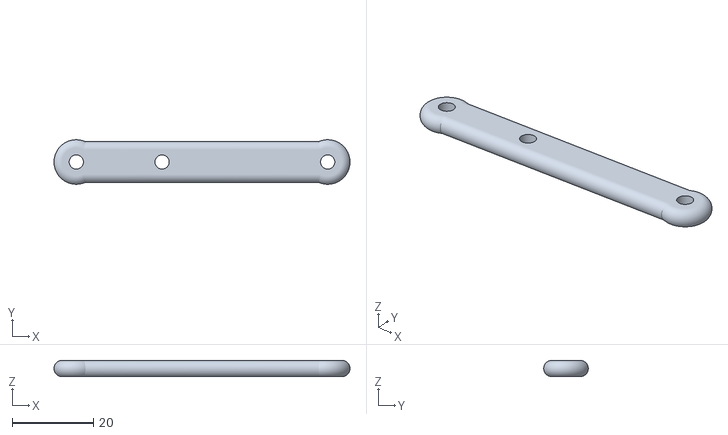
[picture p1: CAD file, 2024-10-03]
Construction/CAD/steering linkage.stl
73.0 x 11.0 x 4.00

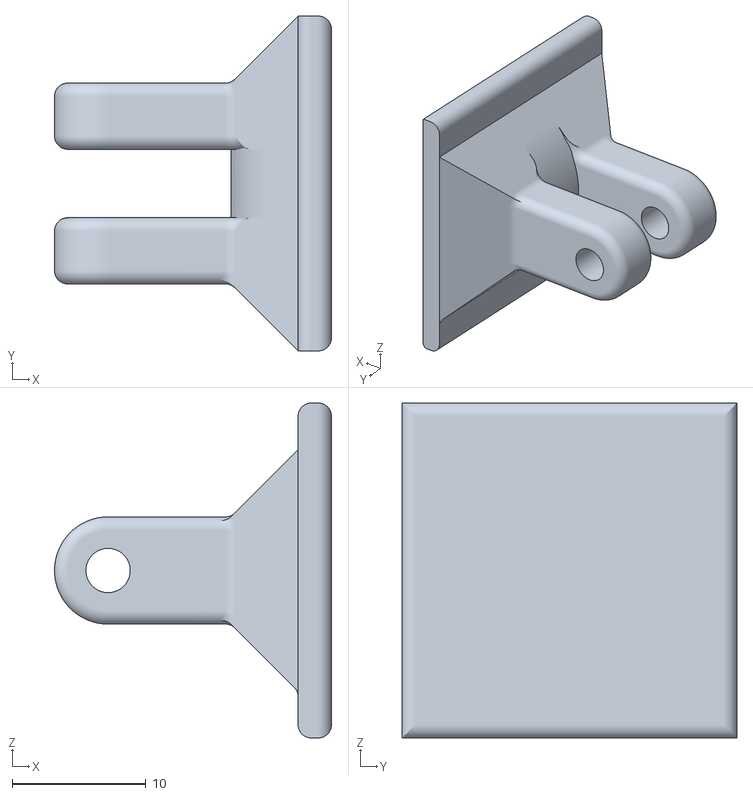
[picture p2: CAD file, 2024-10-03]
Construction/CAD/cam mount.stl
20.7 x 25.0 x 25.0

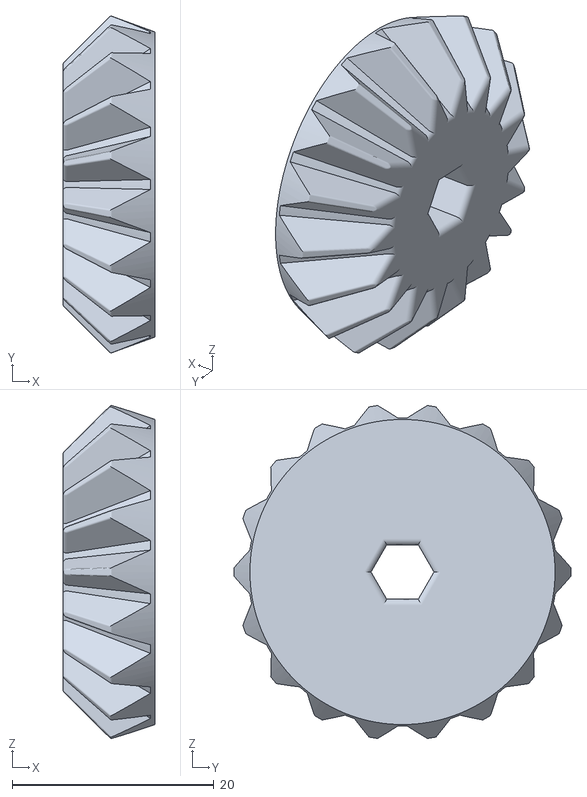
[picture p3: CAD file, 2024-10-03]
Construction/CAD/bevel.stl
9.12 x 33.4 x 33.0

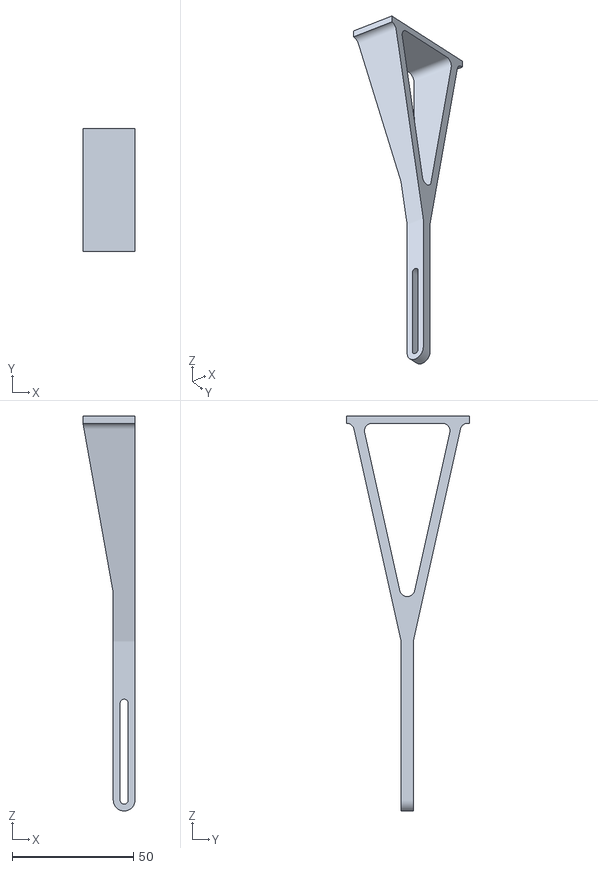
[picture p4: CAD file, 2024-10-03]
Construction/CAD/camera stand.stl
21.5 x 50.6 x 163.0

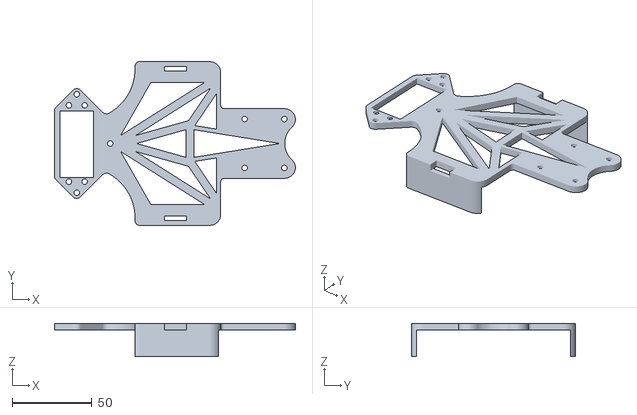
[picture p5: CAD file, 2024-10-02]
Construction/CAD/top plate.stl
151.5 x 102.9 x 20.8

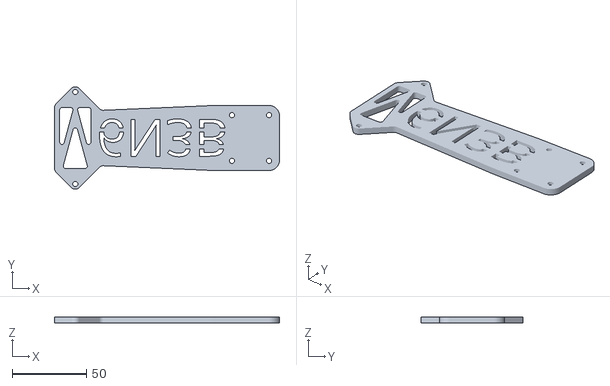
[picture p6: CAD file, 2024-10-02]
Construction/CAD/bottom plate.stl
151.5 x 69.0 x 4.00

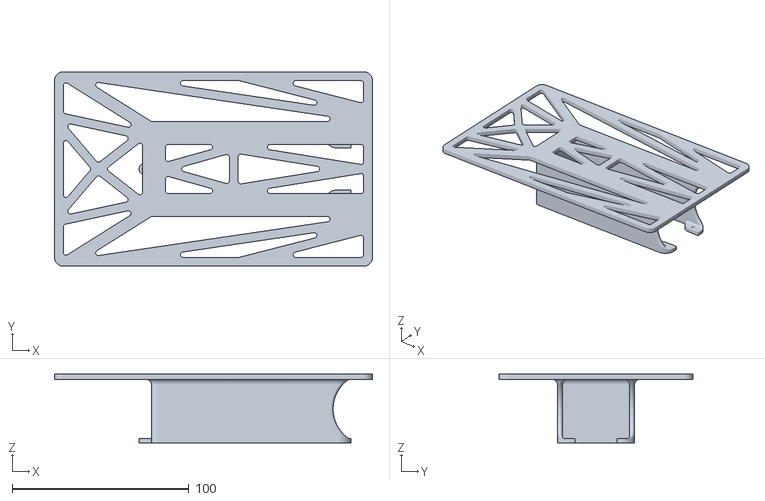
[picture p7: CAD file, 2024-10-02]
Construction/CAD/electronics table.stl
180.0 x 110.0 x 39.0

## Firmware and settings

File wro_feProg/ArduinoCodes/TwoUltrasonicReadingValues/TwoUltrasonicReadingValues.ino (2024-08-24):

//Ultrasonic Sensor with Serial Monitor
int trigger1 = 8;//r
int echo1 = 9;
int trigger2 = 10;//l
int echo2 = 11;
int trigger3 = 12;//f
int echo3 = 13;

float distance1 = 0;
float distance2 = 0;
float distance3 = 0;
float count3 = 0;
float count1 = 0;
float count2 = 0;

void setup() 
{
  pinMode(trigger1, OUTPUT);
  pinMode(echo1, INPUT);
  pinMode(trigger2, OUTPUT);
  pinMode(echo2, INPUT);
  pinMode(trigger3,OUTPUT);
  pinMode(echo3,INPUT);
  Serial.begin(9600);
}

void loop()
{
  // Sensor 1 right
  digitalWrite(trigger1, LOW);
  delayMicroseconds(10);
  digitalWrite(trigger1, HIGH);
  delayMicroseconds(10);
  digitalWrite(trigger1, LOW);
  count1 = pulseIn(echo1, HIGH);
  distance1 = count1 * 0.01715;

  // Sensor 2 left
  digitalWrite(trigger2, LOW);
  delayMicroseconds(10);
  digitalWrite(trigger2, HIGH);
  delayMicroseconds(10);
  digitalWrite(trigger2, LOW);
  count2 = pulseIn(echo2, HIGH);
  distance2 = count2 * 0.01715;

  //sensor 3 center
  digitalWrite(trigger3, LOW);
  delayMicroseconds(10);
  digitalWrite(trigger3, HIGH);
  delayMicroseconds(10);
  digitalWrite(trigger3, LOW);
  count3 = pulseIn(echo3, HIGH);
  distance3 = count3 * 0.01715;

  // Send both distances via Serial
  Serial.print(distance1);
  Serial.print(",");
  Serial.print(distance2);
  Serial.print(",");
  Serial.println(distance3);
  
  delay(10);
}

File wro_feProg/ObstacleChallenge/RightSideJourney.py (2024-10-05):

import time
import board
import busio
import adafruit_bno055
import sys
import serial
sys.path.append('/usr/lib/python3/dist-packages')
import pigpio
from picamera2 import Picamera2, Preview
import cv2
import numpy as np
import parking1 as P
import Blue_detected as b1

# PID controller function for steering
def pid(y, heading, kP):
    # Normalize angles to the range [-180, 180]
    if (y < 360 - y):
        y = y
    elif (y == 360 - y):
        y = 180
    else:
        y = -360 + y

    if (heading < 360 - heading):
        heading = heading
    elif (heading == 360 - heading):
        heading = 180
    else:
        heading = -360 + heading

    # Calculate the error between current heading and desired angle
    if heading < 0 and y < 0:
        error = heading - y
    elif heading < 0 and y > 0:
        error = y + heading
    else:
        error = heading - y

    # Calculate the servo position based on the error
    turn = min(2000, max(1000, 1500 - error * kP))  # Limit the turn value to between 1000 and 2000
    return turn

def main(picam2, pi, sensor):
    # Initialize variables
    heading = roll = pitch = dis = 0.0
    value = 0
    count = 2  # Start count
    arR = arG = yy = xg = xr = 0
    blue = False
    flag = True
    increment = False
    RedB4Turn = False
    orng1 = True
    orng2 = False
    turnThreshold = 350
    redAfterLine = greenAfterLine = False
    s_time = t_time = 0
    cross = False
    invert = False
    redAtTurn = False

    while count < 3:
        # Capture image from the camera
        img = picam2.capture_array()  # Capture the image as a NumPy array
        img1 = img2 = img3 = img  # Duplicate the image for processing
        img = cv2.cvtColor(img, cv2.COLOR_BGR2RGB)  # Convert image color space from BGR to RGB

        # Define color ranges for detection
        lower = (100, 70, 40)  # Lower bound for blue detection
        upper = (145, 255, 175)  # Upper bound for blue detection

        # Detect colors using functions from Blue_detected module
        img1, arR, xr, yr = b1.red_detect(img)  # Detect red color
        img2, arG, xg, yg = b1.green_detect(img)  # Detect green color
        img3, __, __, yy2, h1 = b1.color_detect(img, lower, upper, "blue")  # Detect blue color
        img3, ____, xO, yy, h2 = b1.color_detect(img, np.array([5, 80, 100]), np.array([30, 255, 255]), "orange")  # Detect orange color

        # Set yy based on xO detection
        yy = yy if xO < 340 else 0  # Reset yy if orange is detected beyond threshold

        # Draw a rectangle on the image for visual feedback
        img = cv2.rectangle(img, (0, 100), (640, 350), (255, 255, 255), 2)  # Draw a rectangle on the image
        cv2.imshow("frame", img)  # Display the processed frame

        # Get heading, roll, and pitch from the sensor
        heading, roll, pitch = sensor.euler  # Read euler angles from the sensor
        
        try:
            heading = min(360, max(0, heading))  # Normalize heading
        except:
            heading = 0  # Default to 0 if there's an error
        
        # Try to read distance data from serial
        try:
            dis, distanceRight = map(float, data.split(','))  # Read distance values from serial
        except:
            dis = distanceRight = 0  # Default to 0 if there's an error
        
        # Check for orange color detection
        if (yy > 100 and yy < 320):
            orng1 = True  # First orange detection condition met
            print("orng1")
        elif yy > turnThreshold and orng1:
            orng2 = True  # Second orange detection condition met
            print("orng2")

        # Set blue detection flag if both orange conditions are met
        if orng1 and orng2 and yy2 != 0:
            blue = True  # Set blue detection flag
            print("Blue is true")

        # Control logic based on red and green detection
        if (arR >= 3000 and yr >= 10 and yr > yy) or (arG >= 3000 and yg >= 10 and yg > yy):
            if(int(heading) in range(value, value + 60)):  # Check if heading is in range
                flag = True
                blue = False
                
            # Handle red detection
            if arR > arG:
                if(yr > 120):
                    pi.set_servo_pulsewidth(18, 1800)  # Turn right
                    print("Red_Turning")
                elif(yr > 40):
                    # Glide based on position
                    pi.set_servo_pulsewidth(18, max(1000, min(2000, 1500 + (320 - xr) * (-2))))
                    print("Red_Gliding")
                RedB4Turn = True
                if blue:
                    redAfterLine = True
                    redAtTurn = True
                    greenAfterLine = False
                else:
                    redAtTurn = False
                    
            # Handle green detection
            elif arR < arG:
                if(yg > 120):
                    pi.set_servo_pulsewidth(18, 1200)  # Turn left
                    print("Green_Turning")
                elif(yg > 40):
                    # Glide based on position
                    pi.set_servo_pulsewidth(18, max(1000, min(2000, 1500 + (320 - xg) * (-2))))
                    print("Green_Gliding")
                RedB4Turn = False
                if blue:
                    greenAfterLine = True
                    redAtTurn = False
                    redAfterLine = False

        # Handle blue detection logic
        elif blue:
            if(flag):
                value += 90  # Increment target value for turns
                if value == 360:
                    value = 0  # Reset value after full turn
                    increment = True  # Mark that increment has occurred
                
                if value == 0 and count == 1:
                    s_time = time.time()  # Start timing for parking
                flag = False
                
            if(int(heading) not in range(value, value + 60)):  # Check if heading is outside target range
                orng1 = orng2 = False
                print("turning", heading, value, dis, RedB4Turn)
                if (arR > 3000 and arG < arR) or redAfterLine:  # Condition for red
                    print("redBased")
                    redAfterLine = True
                    greenAfterLine = False
                    if heading >= 330 and value == 90:
                        # Adjust servo based on heading
                        pi.set_servo_pulsewidth(18, max(1000, min(2000, 1500 + (value - (heading - 360)) * 30)))
                    elif value == 0 and heading >= 230:
                        pi.set_servo_pulsewidth(18, max(1000, min(2000, 1500 + (value - (heading - 360)) * 30)))
                    else:
                        pi.set_servo_pulsewidth(18, max(1000, min(2000, 1500 + (value - heading) * 30)))
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

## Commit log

2024-08-24 Create CAD
2024-10-03 Rename mid plate.stl to top plate.stl
    [mid plate.stl, top plate.stl]
